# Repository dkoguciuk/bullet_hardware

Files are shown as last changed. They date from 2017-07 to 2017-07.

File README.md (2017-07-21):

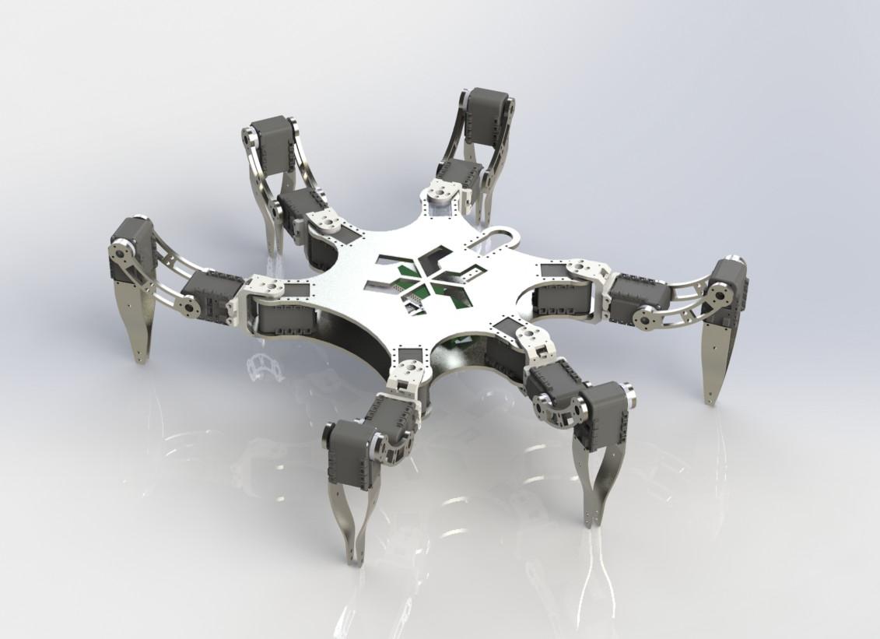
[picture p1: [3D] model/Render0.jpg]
asdasd


# Introduction

This is the project of a six-legged walking robot Bullet named after [bullet ant](http://en.wikipedia.org/wiki/Paraponera_clavata). The project consists of three repositories:
* [bullet_hardware](http://github.com/dkoguciuk/bullet_hardware) - containing 3D model of the robot done with SolidWorks and schematic and layout of PCB boards done with Eagle Software,
* [bullet_firmware](https://github.com/dkoguciuk/bullet_firmware) - containing a low-level program for STM microprocessor written for one of the PCB boards done with CooCox tool,
* [bullet_software](https://github.com/dkoguciuk/bullet_software) - containing a high-level software for onboard RaspberryPi board done with ROS Framework.

# MORE

More information on the [WIKI](http://github.com/dkoguciuk/bullet_software/wiki).

# License

"THE BEER-WARE LICENSE" (Revision 42):  
Above listed contributors are authors of the repositories. As long as you retain this notice you can do whatever you want with this stuff. If we meet some day, and you think this stuff is worth it, you can buy us a beer in return.

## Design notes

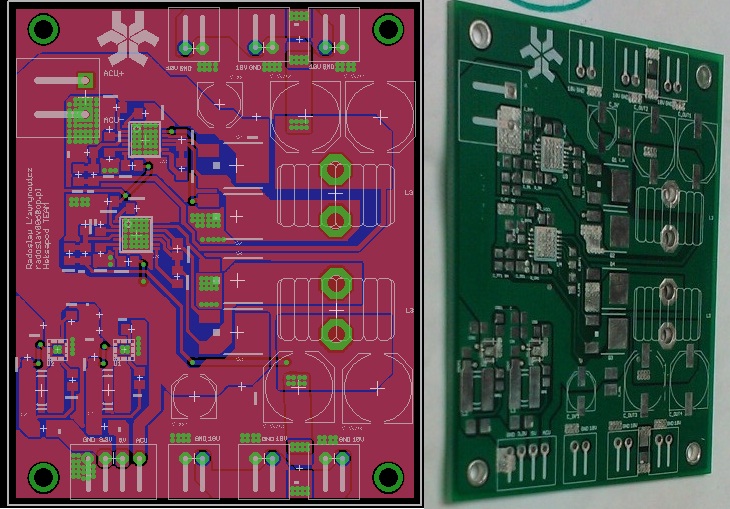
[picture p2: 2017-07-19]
[PCB] power_board/photos/img_fot.jpg

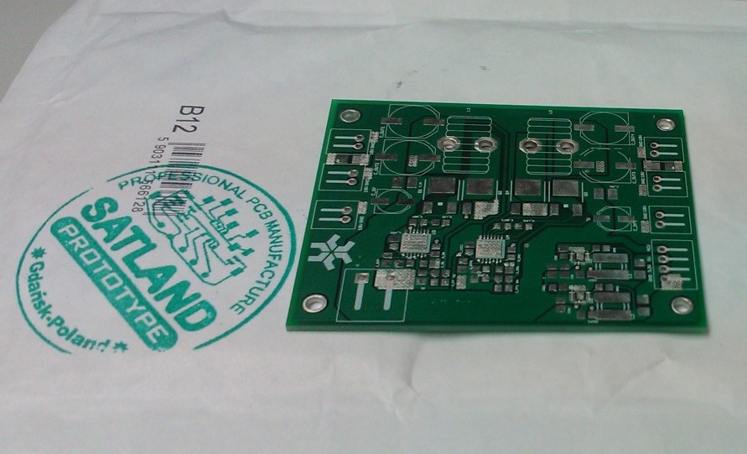
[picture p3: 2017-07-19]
[PCB] power_board/photos/PCB_foto1.jpg

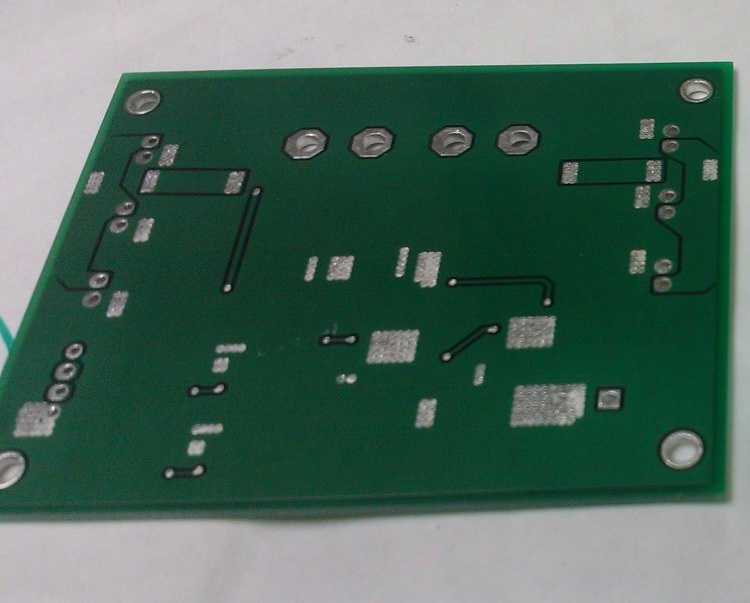
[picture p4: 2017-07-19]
[PCB] power_board/photos/PCB_foto2.jpg

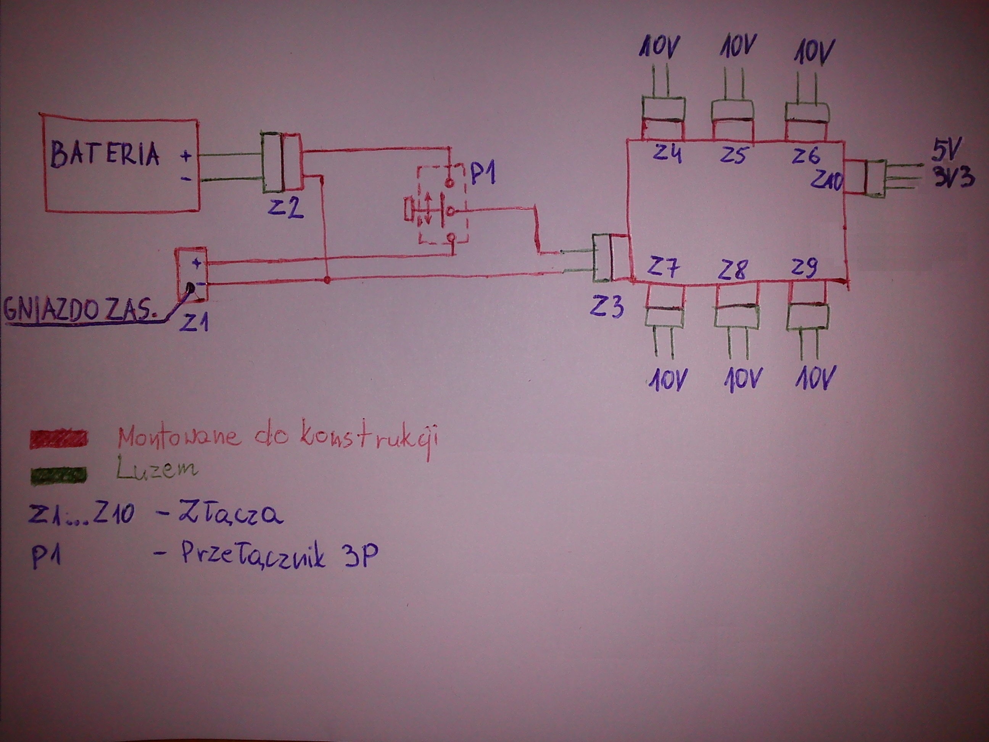
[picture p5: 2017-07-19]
[PCB] power_board/docs/power_sketch.jpg

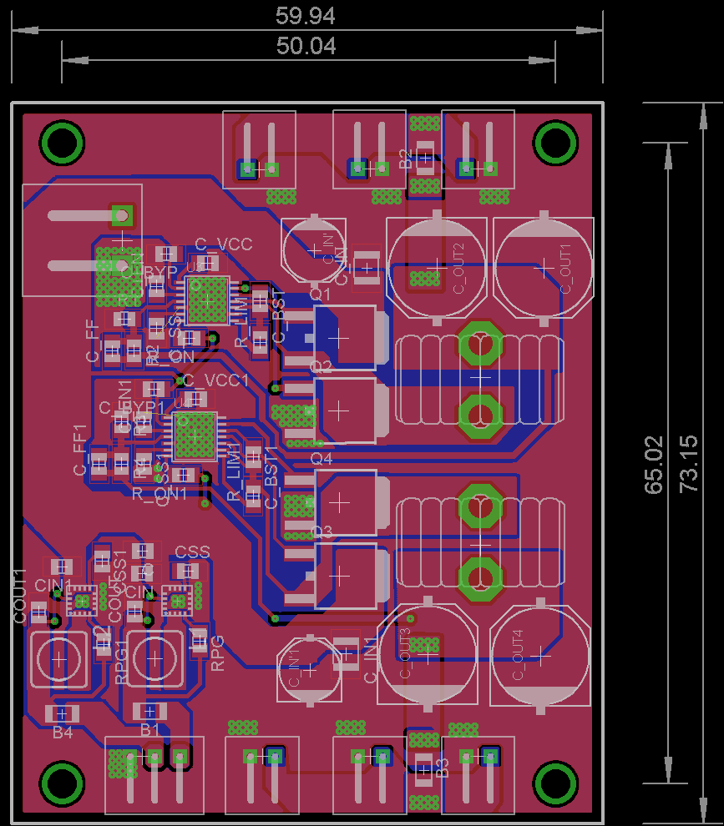
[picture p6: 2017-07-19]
[PCB] power_board/photos/img_płytka.png

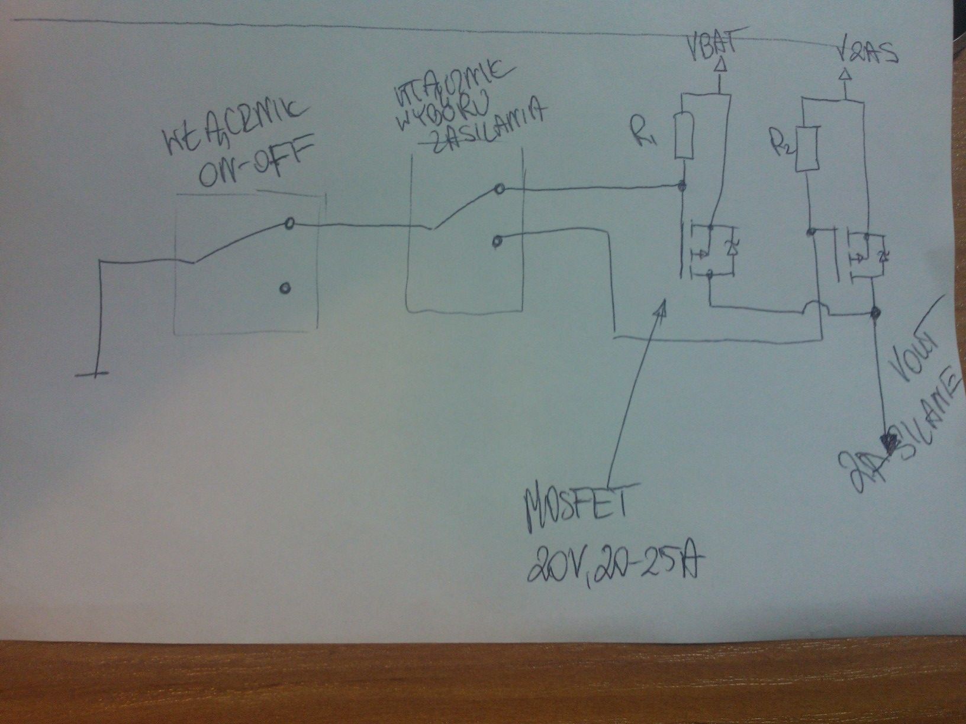
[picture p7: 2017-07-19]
[PCB] power_board/docs/switches_sketch.jpg

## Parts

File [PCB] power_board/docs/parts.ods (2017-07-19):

Nazwa | Element | Ilość | Link
Przełącznik ON-OFF-ON | P1 | 1 | http://www.tme.eu/pl/details/ae-c1720hoaaa/przelaczniki-dzwigniowe/arcolectric/c1720hobbi0ii/
Gniazdo zasilania 10V | Z4-Z9 | 6 | http://www.tme.eu/pl/details/mx-5268-02a/zlacza-spox/molex/0022057025-5268-02a/
Wtyk zasilania 10V | Z4-Z9 | 6 | http://www.tme.eu/pl/details/mx-5264-02/zlacza-spox/molex/0050375023-5264-02/#
Gniazdo zasilania 3.3V / 5V | Z10 | 1 | http://www.tme.eu/pl/details/mx-5268-03a/zlacza-spox/molex/0022057035-5268-03a/#
Wtyk zasilania 3.3V / 5V | Z10 | 1 | http://www.tme.eu/pl/details/mx-5264-03/zlacza-spox/molex/0050375033-5264-03/#
Styki wtyków 10V / 5V / 3.3V | Z4-Z10 | 15 | http://www.tme.eu/pl/details/mx-5263-pbtl/zlacza-spox/molex/0008701040-5263pbtl/#
Gniazdo zasilania wejściowe | Z3 | 1 | http://www.tme.eu/pl/details/2edgrc-5.0-02p14/listwy-zaciskowe-do-druku/degson-electronics/2edgrc-50-02p-14-00ah/
Wtyk zasilania wejściowego | Z3 | 1 | http://www.tme.eu/pl/details/2edgk5.00-02p14/listwy-zaciskowe-do-druku/degson-electronics/2edgk-500-02p-14/
Gniazdo + Wtyk zasilacza | Z1 | 1 | http://riku.pl/towar/p/id/1530/kontekst/4206/
Bezpiecznik 3.3V / 5V | B1 | 2 | http://www.tme.eu/pl/details/3413.0222.11/bezpieczniki-smd-1206-szybkie/schurter/#
Bezpiecznik 10V | B2,B3 | 2 | http://www.tme.eu/pl/details/3413.0328.11/bezpieczniki-smd-1206-zwloczne/schurter/#
 |  |  |  | ??

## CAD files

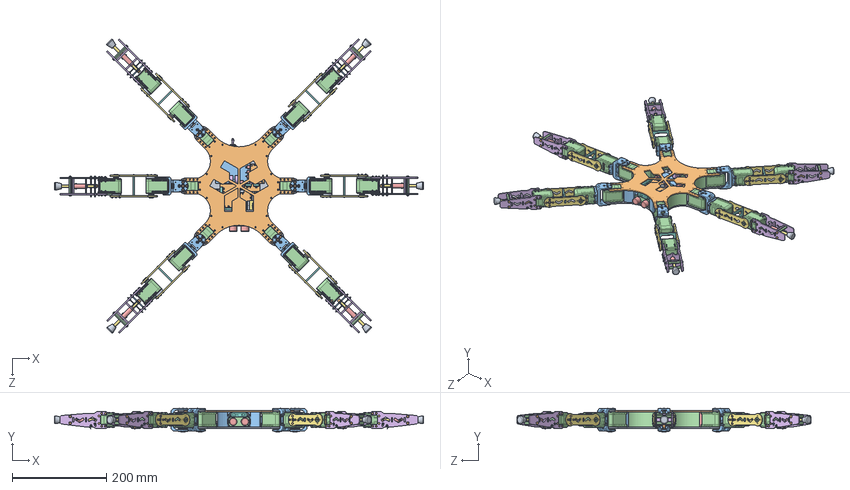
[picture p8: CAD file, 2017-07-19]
[3D] model/Bullet.SLDASM
784.4 x 50.1 x 625.7 mm
body_down
body_up
ax12_plastic_a x 6
ax12_body x 18
ax12_wheel x 18
ax12_cover x 72
ax12_connector x 36
ax12_insert x 18
ax12_horn x 18
ax12_screw x 18
ax12_plastic_b x 6
ax12_sleave x 18
ax12_ring x 18
forearm x 12
arm x 12
arm_strut x 6
omron_actuator x 6
omron_base x 6
rod_switch x 12
bushing x 12
sleeve_external x 6
forearm_strut x 12
sleeve_internal x 6
spring x 6
antislipper x 6
pan head cross recess screw_iso x 222
hex thin nut chamfered gradeab_iso x 72
sonar_pcb
sonar_transducer x 2
sonar_smt x 3
sonar_capacitor x 6
sharp_body
sharp_board
sharp_connector
plug_front
plug_side x 4
plug_rear
switch
switch_nut
imu_goldpin
imu_connector
imu_board
power_pcb
power_connector
power_molex_2 x 6
power_coil x 2
rpi_pcb
rpi_usb_5v
rpi_sd
rpi_gpio
rpi_usb_2x
rpi_lan
rpi_rca
rpi_jack
rpi_hdmi
stm_molex_4 x 9
stm_molex_3 x 5
stm_brd

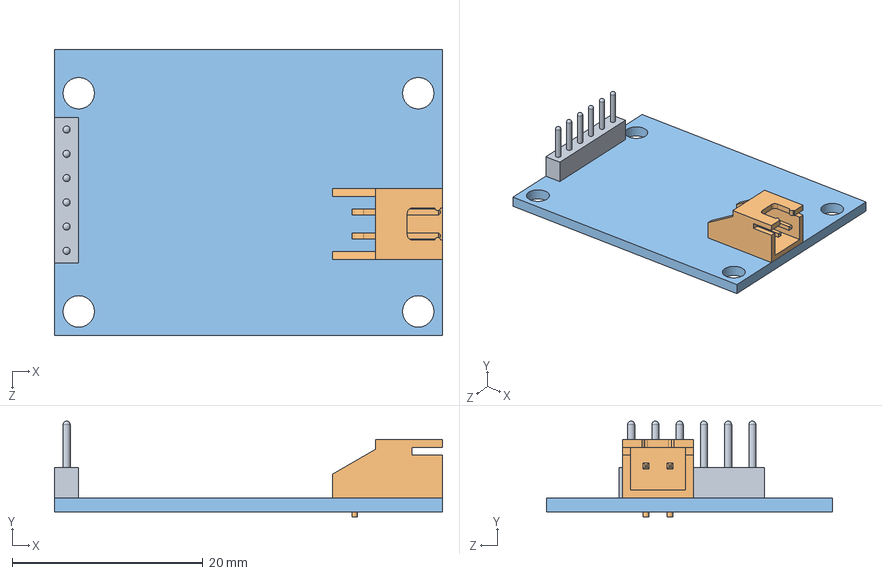
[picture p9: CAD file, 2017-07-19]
[3D] model/Electronics/IMU/imu.SLDASM
40.6 x 10.1 x 30.0 mm
imu_goldpin
imu_connector
imu_board

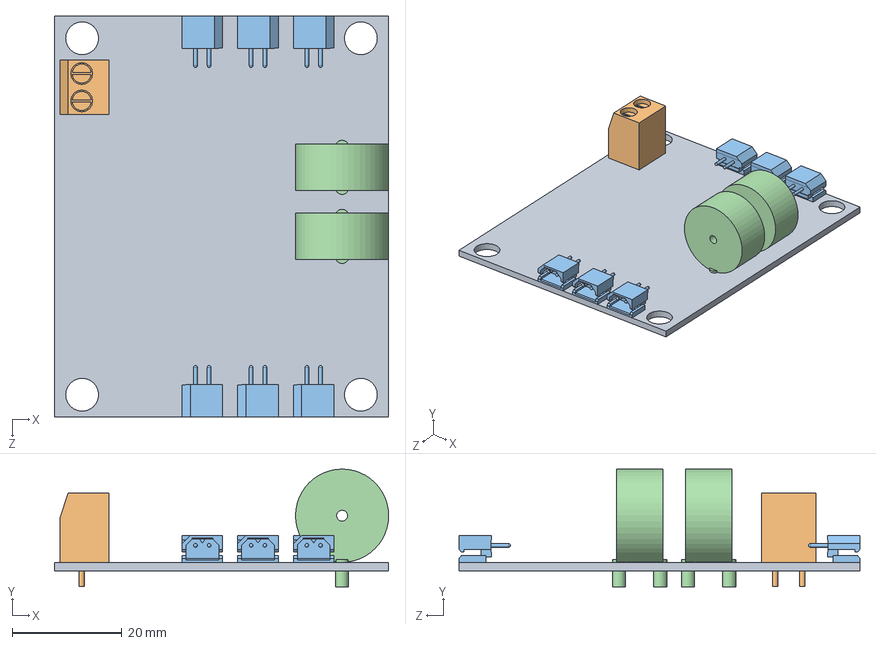
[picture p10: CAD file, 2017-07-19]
[3D] model/Electronics/PowerSupply/power_supply.SLDASM
61.0 x 21.5 x 73.2 mm
power_pcb
power_connector
power_molex_2 x 6
power_coil x 2

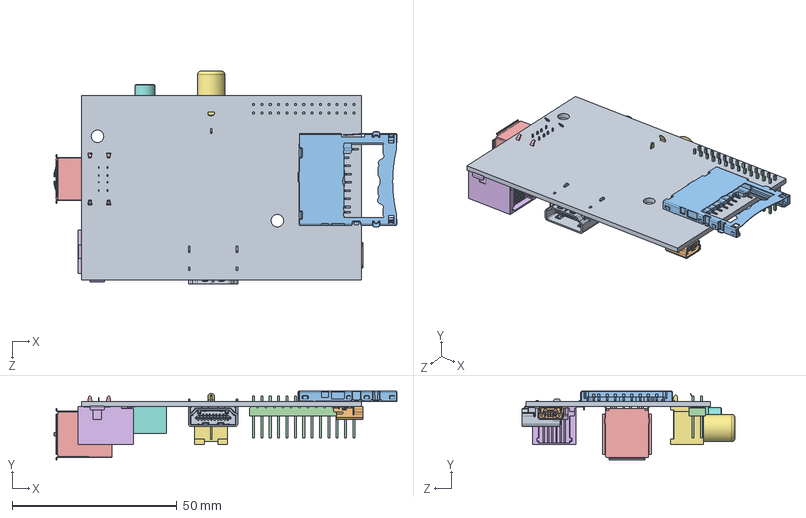
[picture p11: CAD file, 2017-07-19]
[3D] model/Electronics/RPI/rpi.SLDASM
104.1 x 20.9 x 64.6 mm
rpi_pcb
rpi_usb_5v
rpi_sd
rpi_gpio
rpi_usb_2x
rpi_lan
rpi_rca
rpi_jack
rpi_hdmi

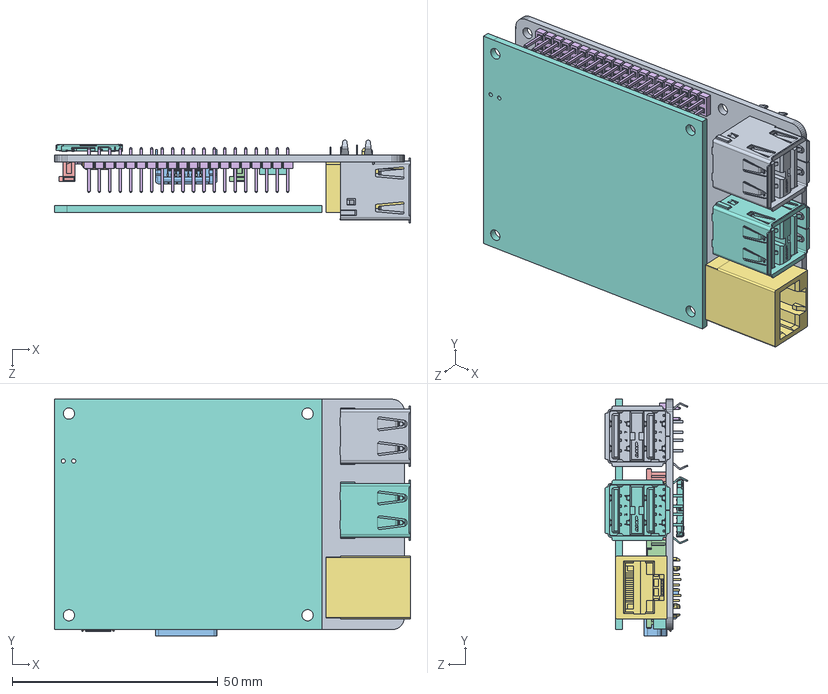
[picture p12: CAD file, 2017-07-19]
[3D] model/Electronics/RPI2/RPIBPlus.SLDASM
86.5 x 57.5 x 20.1 mm
Board
User_Library-0805_SMD_Resistor x 3
RES0402 x 53
CAPC1005X55N_EIA_0402 x 22
CAPC2012X90N_EIA_0805 x 12
CAPC3216X140N_EIA_1206
CAPC1608X55N_EIA_0603 x 4
c-2201778-1-a-3d
SMSCLAN9514
micro_usb
CSI
DSI
Samtec-TSW-120-07-F-D
USB
USB2
Extruded x 4
Extruded_2
Extruded_3 x 2
Extruded_4 x 2
Extruded_5
Extruded_6 x 2
Extruded_7
Extruded_8
Extruded_9 x 2
Extruded_10
Extruded_11
Extruded_12
Extruded_13 x 2
Extruded_14
BoardHelp

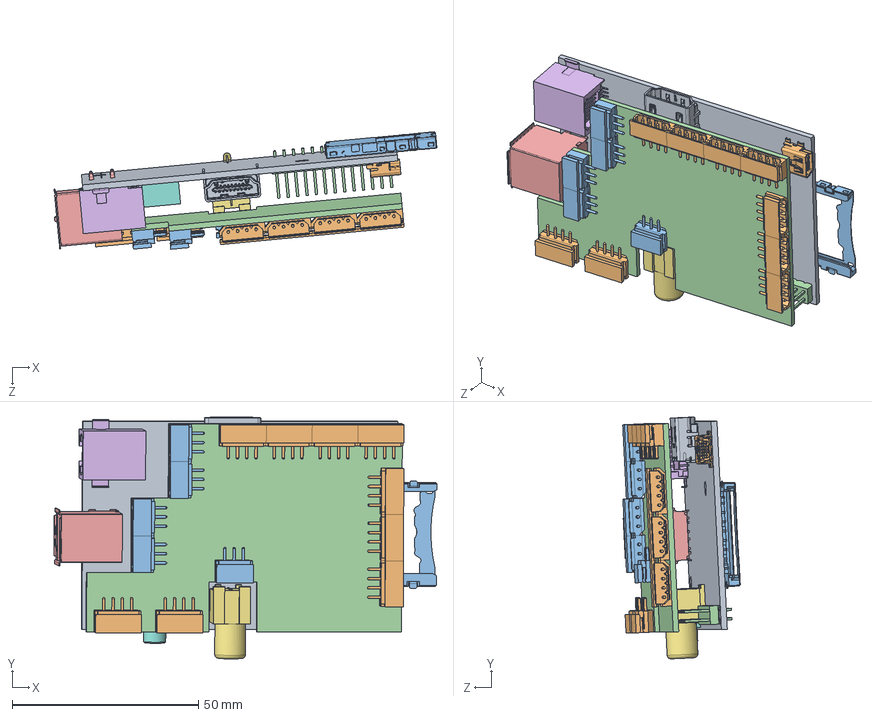
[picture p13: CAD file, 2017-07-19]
[3D] model/Electronics/STM/stm.SLDASM
102.9 x 65.0 x 31.6 mm
rpi_pcb
rpi_usb_5v
rpi_sd
rpi_gpio
rpi_usb_2x
rpi_lan
rpi_rca
rpi_jack
rpi_hdmi
stm_molex_4 x 9
stm_molex_3 x 5
stm_brd

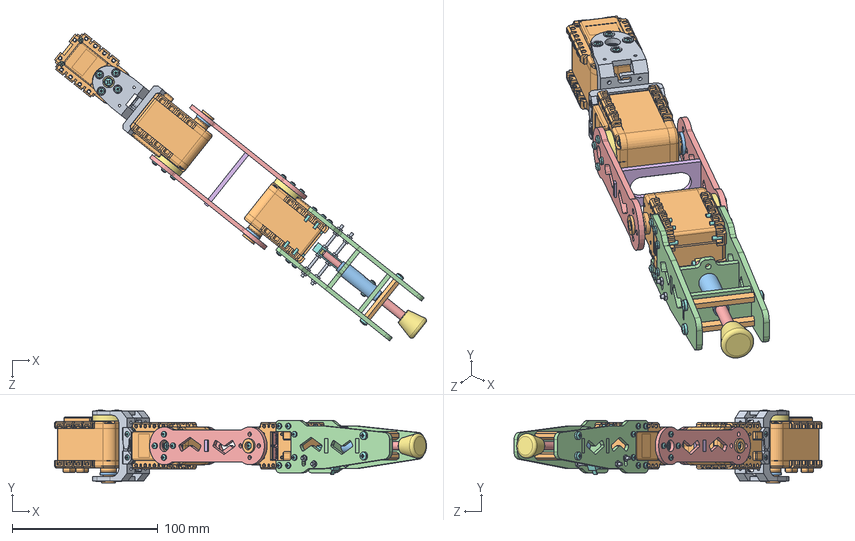
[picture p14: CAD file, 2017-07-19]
[3D] model/Leg/leg.SLDASM
255.4 x 50.1 x 211.4 mm
ax12_plastic_a
ax12_body x 3
ax12_wheel x 3
ax12_cover x 12
ax12_connector x 6
ax12_insert x 3
ax12_horn x 3
ax12_screw x 3
ax12_plastic_b
ax12_sleave x 3
ax12_ring x 3
forearm x 2
arm x 2
arm_strut
omron_actuator
omron_base
rod_switch x 2
bushing x 2
sleeve_external
forearm_strut x 2
sleeve_internal
spring
antislipper
pan head cross recess screw_iso x 37
hex thin nut chamfered gradeab_iso x 12

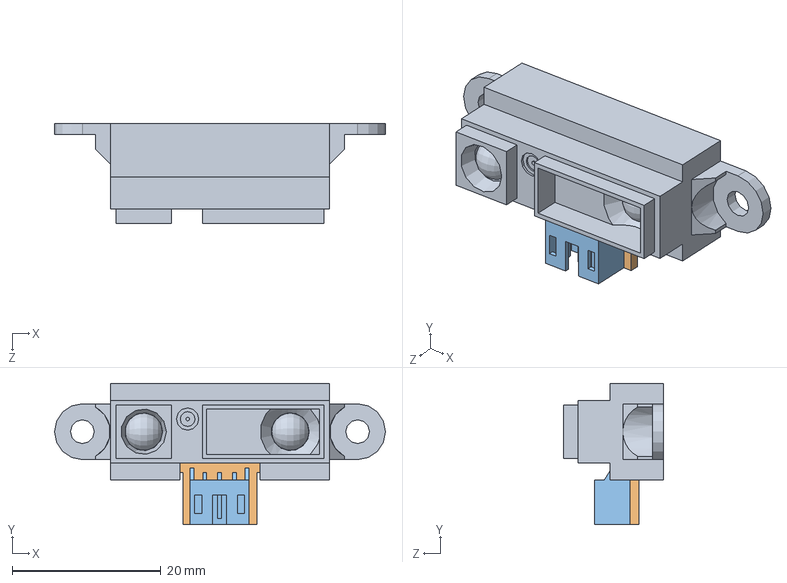
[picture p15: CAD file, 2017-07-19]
[3D] model/Electronics/Sharp/sharp.sldasm
44.5 x 19.0 x 13.5 mm
sharp_body
sharp_board
sharp_connector

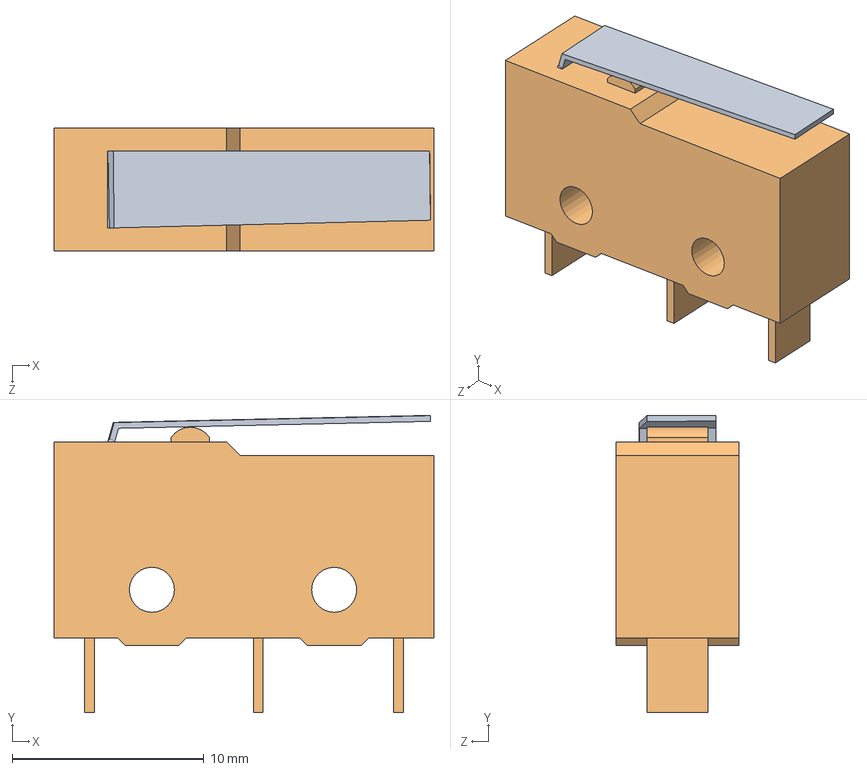
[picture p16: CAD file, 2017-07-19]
[3D] model/Leg/Omron/omron.SLDASM
19.8 x 15.5 x 6.40 mm
omron_actuator
omron_base

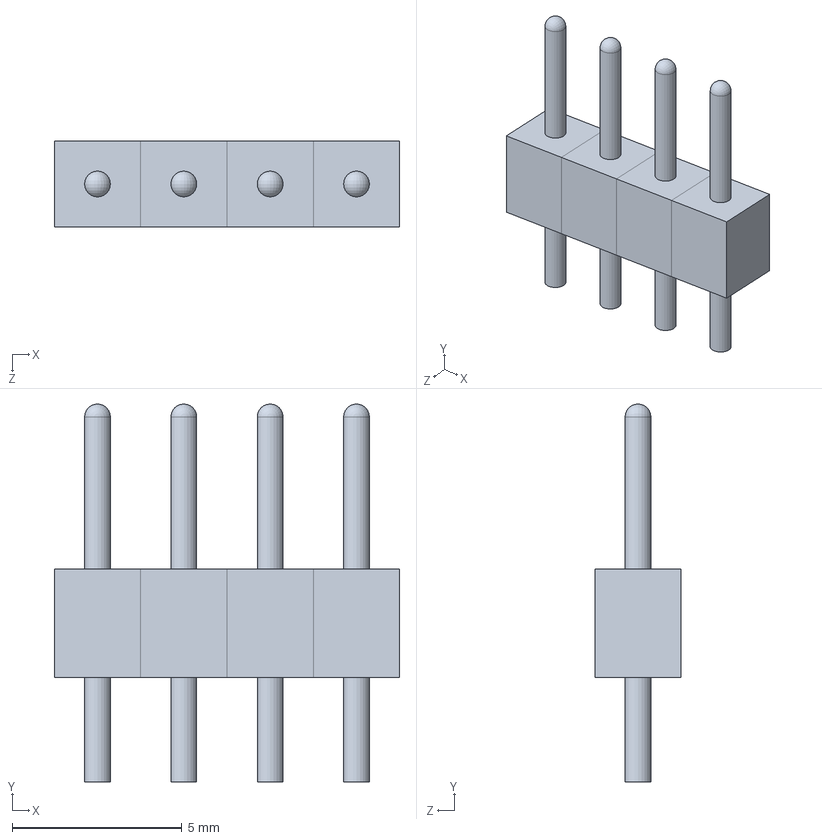
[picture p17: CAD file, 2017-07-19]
[3D] model/Electronics/STM/Parts/stm_goldpin_4.SLDASM
10.2 x 11.1 x 2.54 mm
GoldPin1x x 4

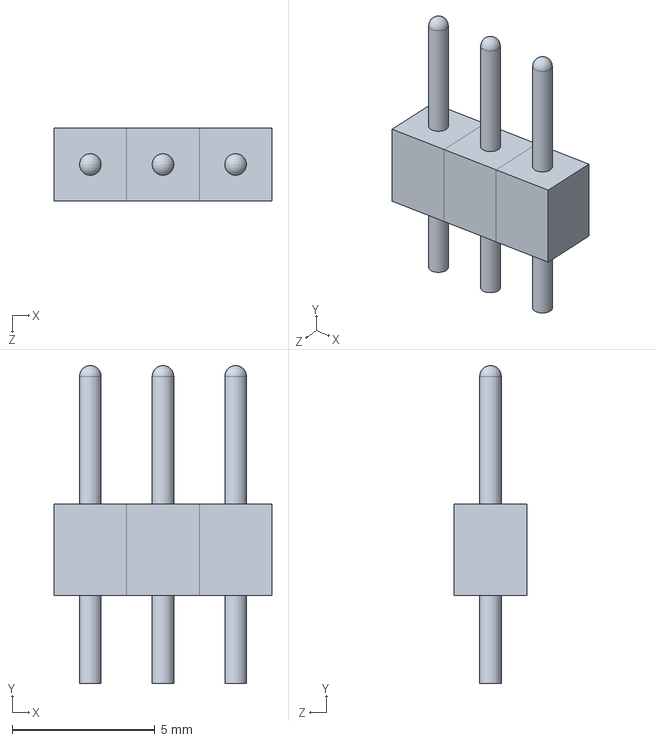
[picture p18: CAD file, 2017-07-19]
[3D] model/Electronics/STM/Parts/stm_goldpin_3.SLDASM
7.62 x 11.1 x 2.54 mm
GoldPin1x x 3

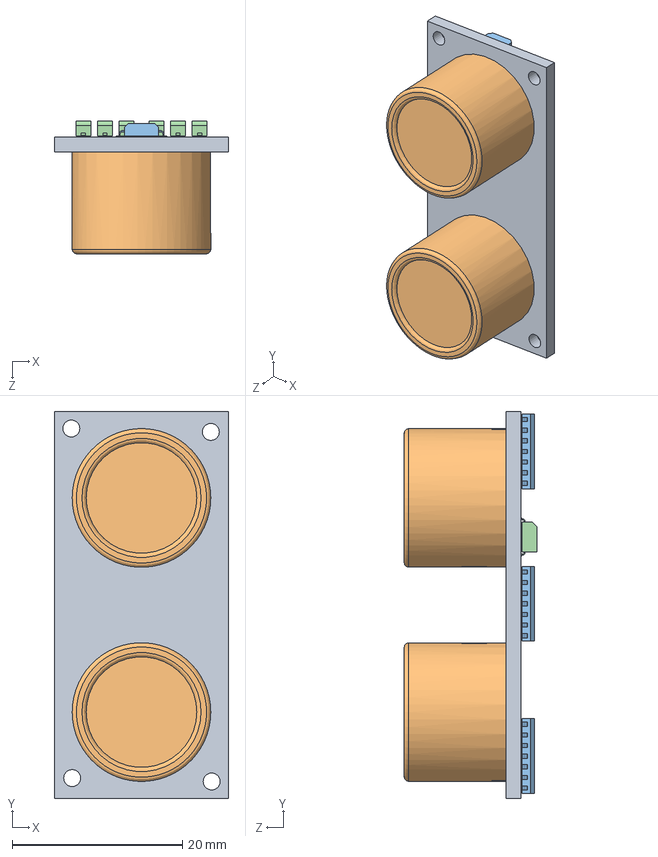
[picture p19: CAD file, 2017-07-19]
[3D] model/Electronics/Sonar/sonar.SLDASM
20.5 x 45.5 x 15.6 mm
sonar_pcb
sonar_transducer x 2
sonar_smt x 3
sonar_capacitor x 6

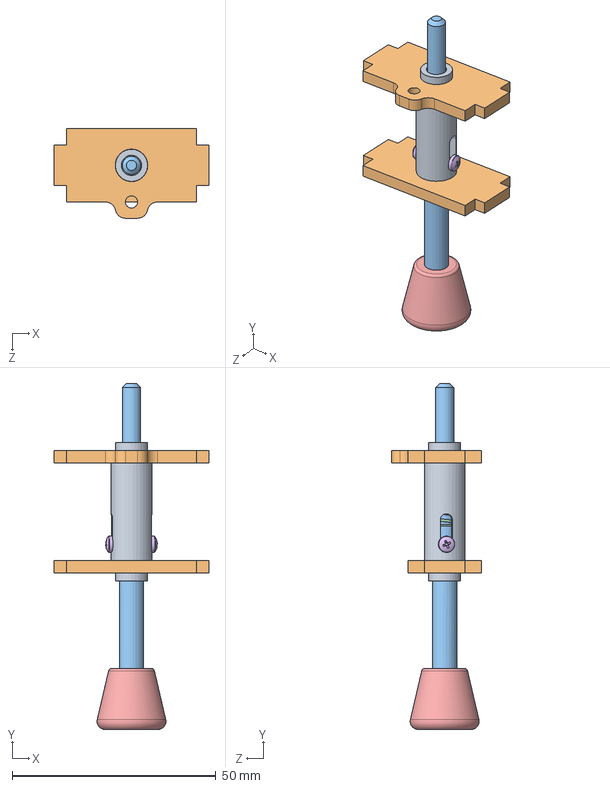
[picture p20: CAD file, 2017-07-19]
[3D] model/Leg/Absorber/absorber.SLDASM
38.0 x 85.0 x 22.0 mm
sleeve_external
forearm_strut x 2
sleeve_internal
spring
antislipper
pan head cross recess screw_iso x 2

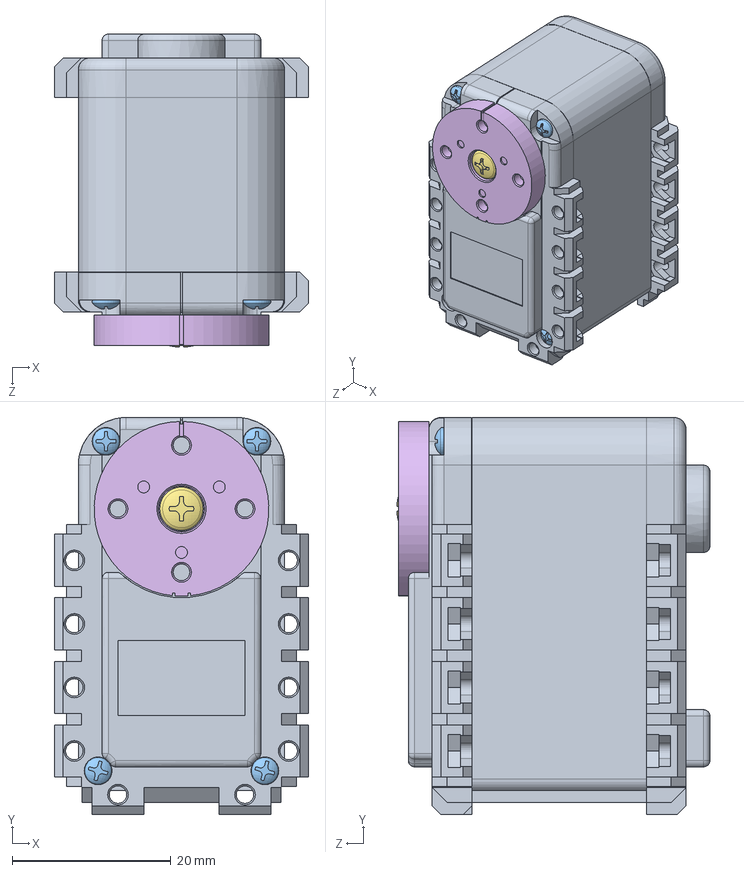
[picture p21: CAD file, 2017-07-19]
[3D] model/Leg/AX-12A/ax12.SLDASM
32.0 x 50.0 x 39.4 mm
ax12_body
ax12_wheel
ax12_cover x 4
ax12_connector x 2
ax12_insert
ax12_horn
ax12_screw

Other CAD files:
[3D] model/Electronics/RPI2/Parts/HDMI.sldasm
[3D] model/Electronics/RPI2/Parts/Ethernet.sldasm
[3D] model/Electronics/RPI2/Parts/Free-Models.sldasm
[3D] model/CAM/arm_strut_final_3.dxf
[3D] model/Body/body_down.SLDPRT
[3D] model/Body/body_up.SLDPRT
[3D] model/Body/plug_front.sldprt
[3D] model/Body/plug_rear.sldprt
[3D] model/Body/plug_side.sldprt
[3D] model/Body/switch.SLDPRT
[3D] model/Body/switch_nut.SLDPRT
[3D] model/CAM/arm_final_3.dxf
[3D] model/CAM/body_bottom_final_3.dxf
[3D] model/CAM/body_top_final_3.dxf
[3D] model/CAM/forearm_final_3.dxf
[3D] model/CAM/forearm_strut_A_final_3.dxf
[3D] model/CAM/forearm_strut_B_final_3.dxf
[3D] model/CAM/sleeve_external_final_3.dxf
[3D] model/CAM/sleeve_internal_final_3.dxf
[3D] model/Electronics/Battery/battery.SLDPRT
[3D] model/Electronics/IMU/Parts/imu_board.SLDPRT
[3D] model/Electronics/IMU/Parts/imu_connector.SLDPRT
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

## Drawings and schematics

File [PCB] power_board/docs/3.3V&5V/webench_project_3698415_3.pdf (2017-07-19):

# WEBENCH® Power Architect

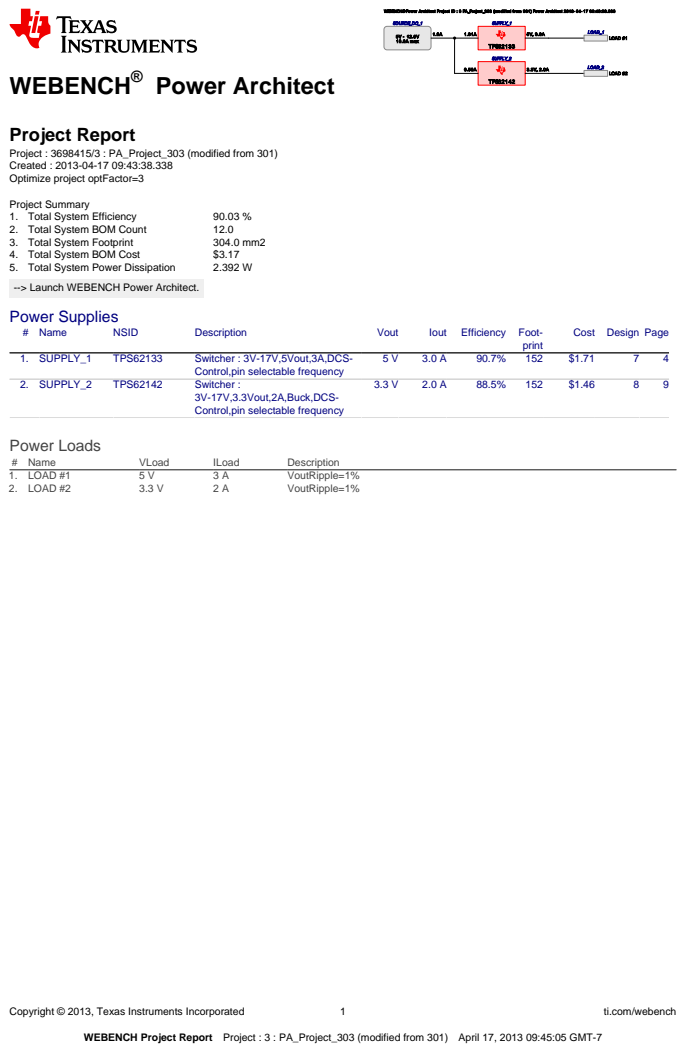
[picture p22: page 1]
Copyright © 2013, Texas Instruments Incorporated; ti.com/webench; 1. Total System Efficiency; 2. Total System BOM Count; 3. Total System Footprint; 4. Total System BOM Cost; 5. Total System Power Dissipation; LOAD_1; LOAD #1; TPS62133; SUPPLY_1; LOAD_2; LOAD #2; TPS62142; SUPPLY_2; 9V - 12.6V 10.0A max; SOURCE_DC_1; # Name; NSID; Description; Vout; Iout Efficiency Foot-; print; 1. SUPPLY_1; Switcher : 3V-17V,5Vout,3A,DCS-; 2. SUPPLY_2; Switcher :; Power Loads; VLoad; ILoad; 1. LOAD #1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

WEBENCH® Power Architect Project ID : 3 PA_Project_303 (modified from 301) Power Architect 2013- 04- 17 09:43:38.338

Project Report
Project : 3698415/3 : PA_Project_303 (modified from 301)
Created : 2013-04-17 09:43:38.338
Optimize project optFactor=3

Project Summary
--> Launch WEBENCH Power Architect. (http://webench.ti.com/webench5/power/webench5.cgi?app=powerarchitect&project_id=3)
Power Supplies

Cost Design Page

Control,pin selectable frequency

3V-17V,3.3Vout,2A,Buck,DCS-

WEBENCH Project Report Project : 3 : PA_Project_303 (modified from 301) April 17, 2013 09:45:05 GMT-7

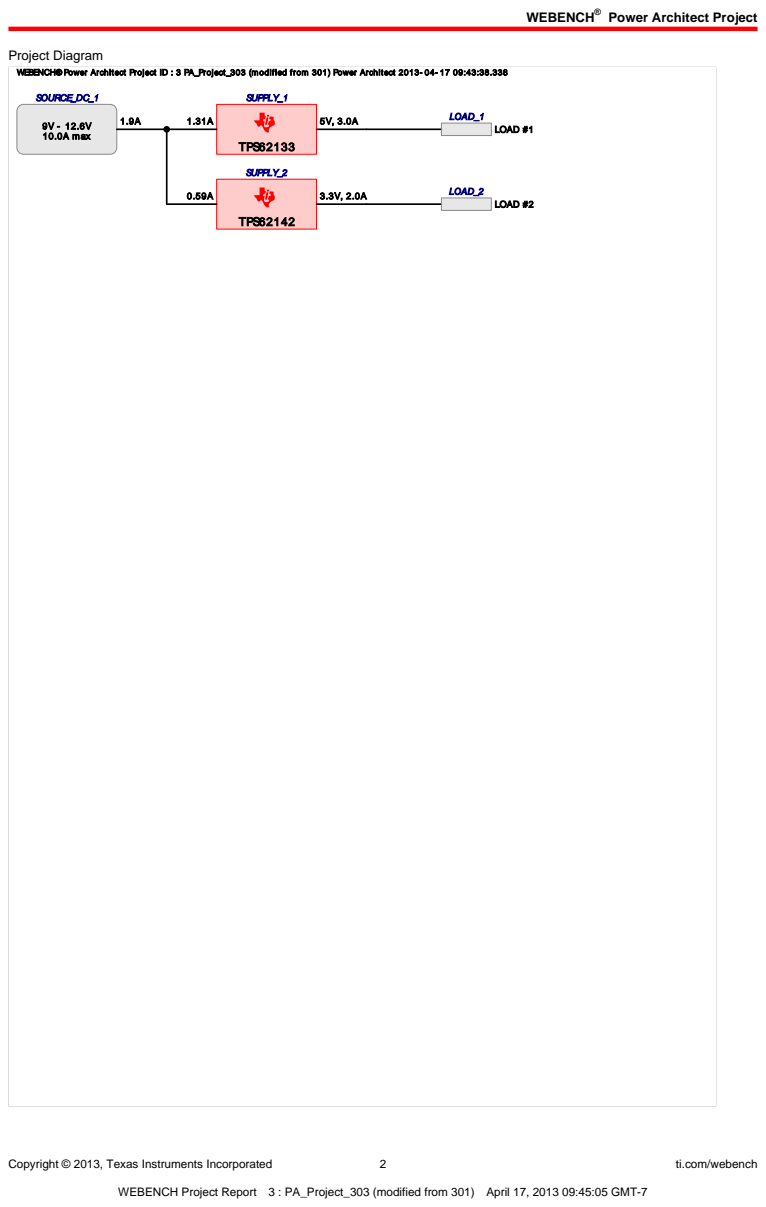
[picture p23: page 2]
WEBENCH®; Copyright © 2013, Texas Instruments Incorporated; ti.com/webench; Project Diagram; LOAD_1; LOAD #1; TPS62133; SUPPLY_1; LOAD_2; LOAD #2; TPS62142; SUPPLY_2; 9V - 12.6V 10.0A max; SOURCE_DC_1

Power Architect Project

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

WEBENCH Project Report 3 : PA_Project_303 (modified from 301) April 17, 2013 09:45:05 GMT-7

Copyright © 2013, Texas Instruments Incorporated | 3 | ti.com/webench

### Electrical Procurement BOM

Manufacturer | Part Number | Description | Quantity Budgetary Price | Footprint
(mm²
)
Kemet | C0805C332K5RACTU | 0805 | 2 | $0.01 | 26
TDK | C2012X5R0J226M | 0805 | 1 | $0.06 | 13
Vishay-Dale | CRCW0402100KFKED | 0402 | 2 | $0.01 | 15
MuRata | GRM31CR61E106KA12L | 1206 | 2 | $0.07 | 37
Taiyo Yuden | LMK212BJ226MG-T | 0805 | 1 | $0.12 | 13
Bourns | SRN6045-2R2Y | SRN6045 | 1 | $0.16 | 64
Texas Instruments | TPS62133RGTR | S-PVQFN-N16 | 1 | $1.30 | 36
Texas Instruments | TPS62142RGTR | S-PVQFN-N16 | 1 | $1.15 | 36
TDK | VLC6045T-2R2N | VLC6045 | 1 | $0.20 | 64
Total | | | 12 | $3.17 | 304

## WEBENCH ® Design Report

## TPS62133

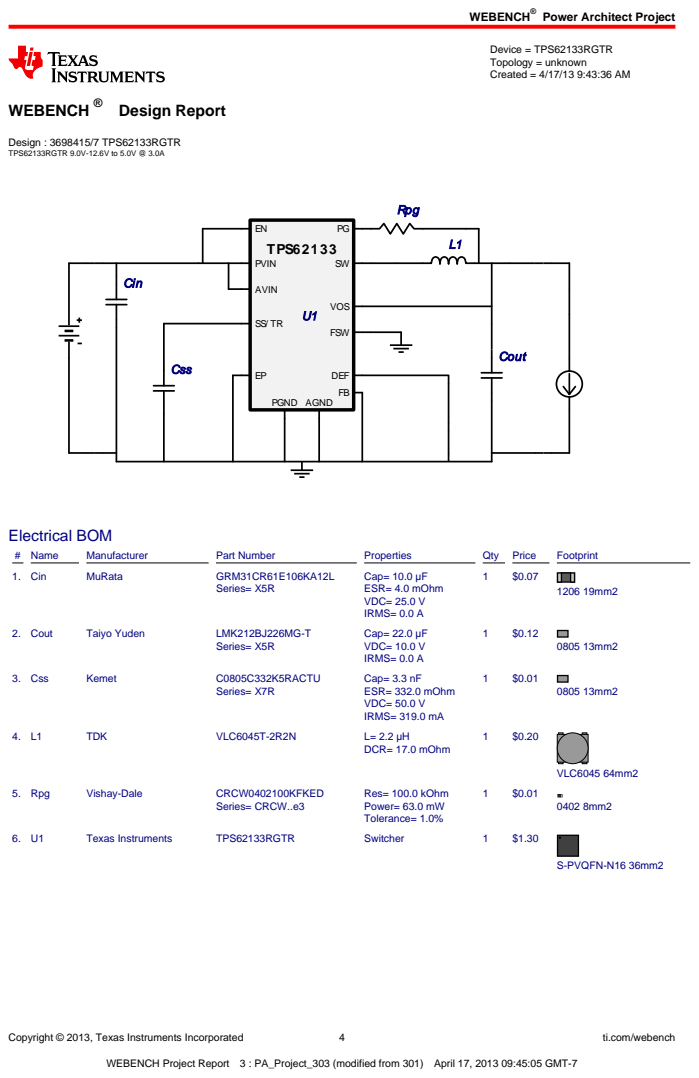
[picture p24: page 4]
Copyright © 2013, Texas Instruments Incorporated; ti.com/webench; Design : 3698415/7 TPS62133RGTR TPS62133RGTR 9.0V-12.6V to 5.0V @ 3.0A; Device = TPS62133RGTR Topology = unknown Created = 4/17/13 9:43:36 AM; Cin; Cout; Css; Rpg; AGND; FSW; DEF; AVIN; PVIN; VOS; PGND; Electrical BOM; # Name; Manufacturer; Part Number; Properties; Qty Price; Footprint; 1. Cin; MuRata; GRM31CR61E106KA12L; Series= X5R; Cap= 10.0 µF ESR= 4.0 mOhm VDC= 25.0 V IRMS= 0.0 A; 2. Cout; Taiyo Yuden; LMK212BJ226MG-T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

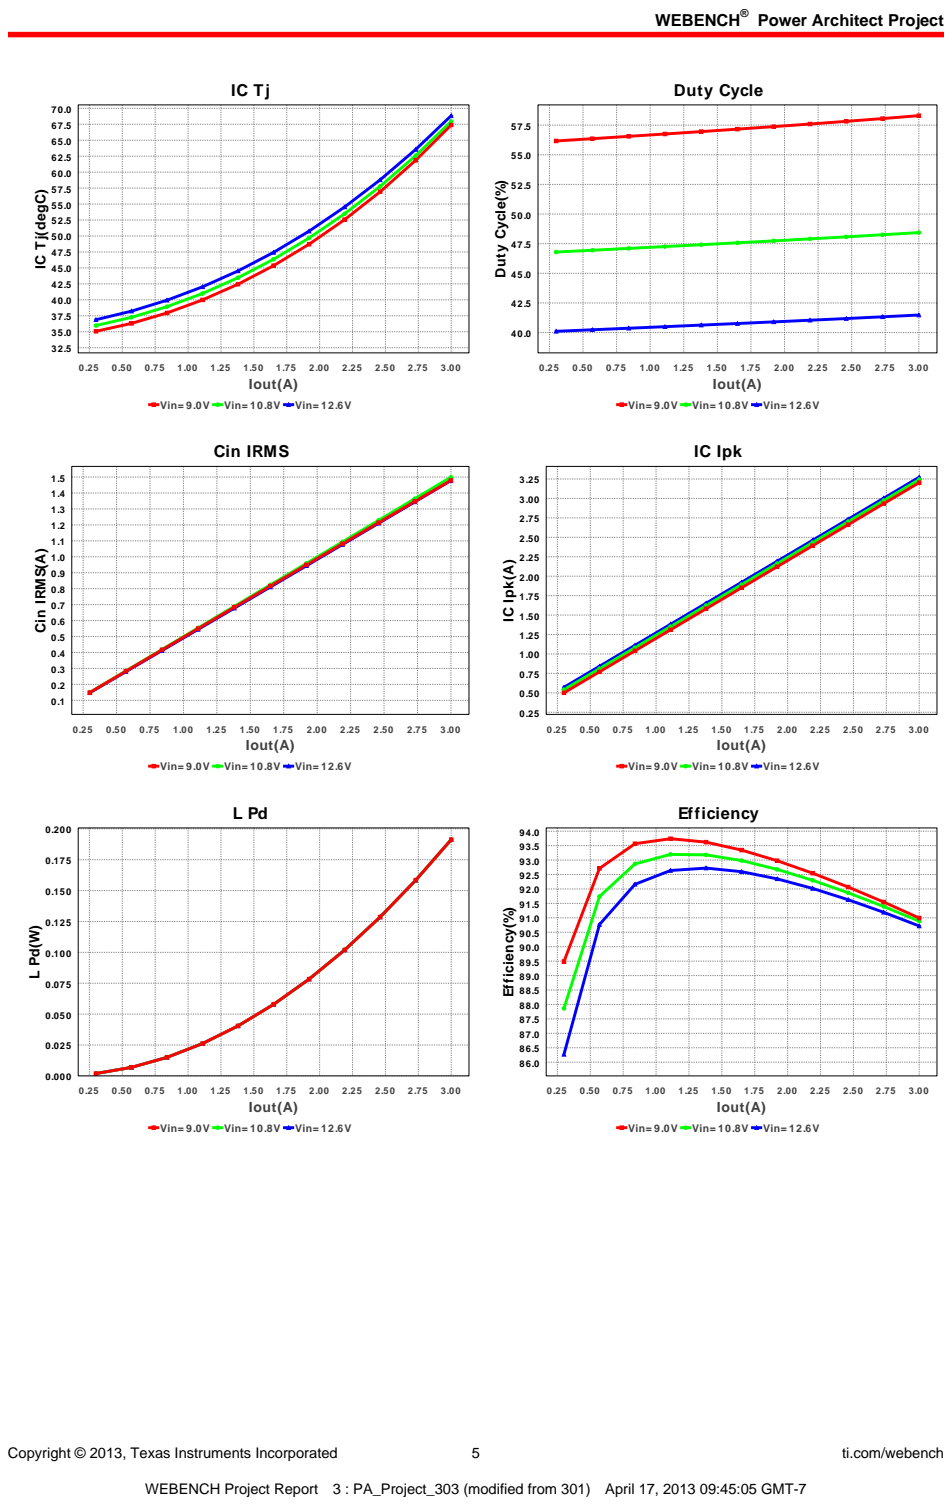
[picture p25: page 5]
Copyright © 2013, Texas Instruments Incorporated; ti.com/webench; 0.25 0.50 0.75 1.00 1.25 1.50 1.75 2.00 2.25 2.50 2.75 3.00 Iout(A); Duty Cycle; Iout(A); Duty Cycle(%); Cin IRMS; Cin IRMS(A); IC Ipk; IC Ipk(A); Efficiency; Efficiency(%)

IC Tj(degC)

Vin= 9.0V Vin= 10.8V Vin= 12.6V

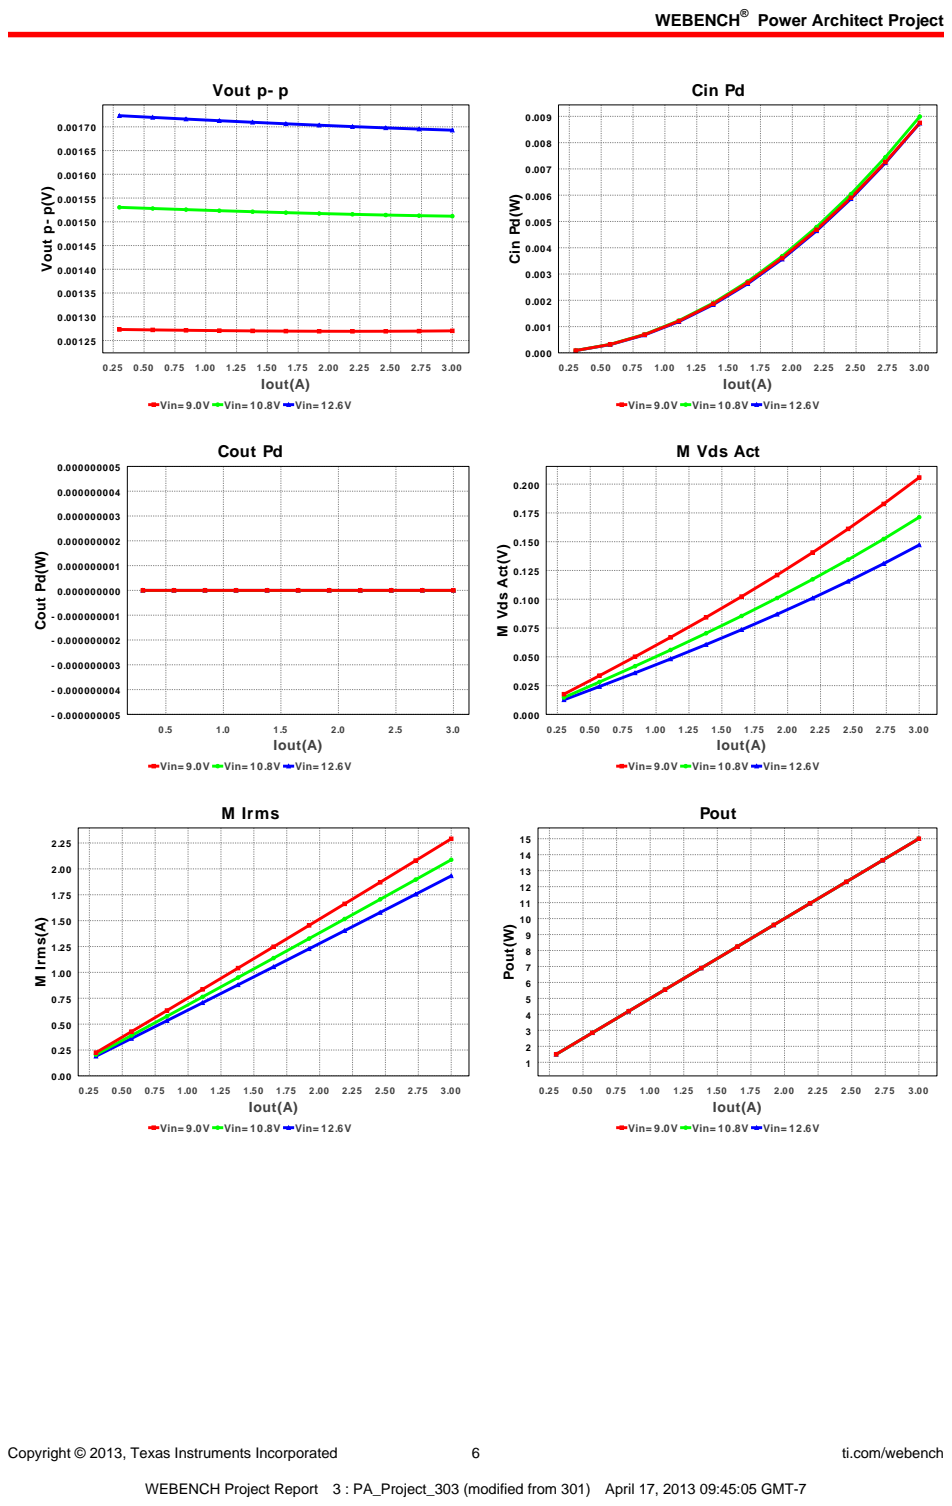
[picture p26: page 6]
Copyright © 2013, Texas Instruments Incorporated; ti.com/webench; Vout p- p; 0.25 0.50 0.75 1.00 1.25 1.50 1.75 2.00 2.25 2.50 2.75 3.00 Iout(A); Vout p- p(V); Cin Pd; Cin Pd(W); Cout Pd; Iout(A); Cout Pd(W); M Vds Act; M Vds Act(V); M Irms; M Irms(A); Pout; Pout(W)

Vin= 9.0V Vin= 10.8V Vin= 12.6V

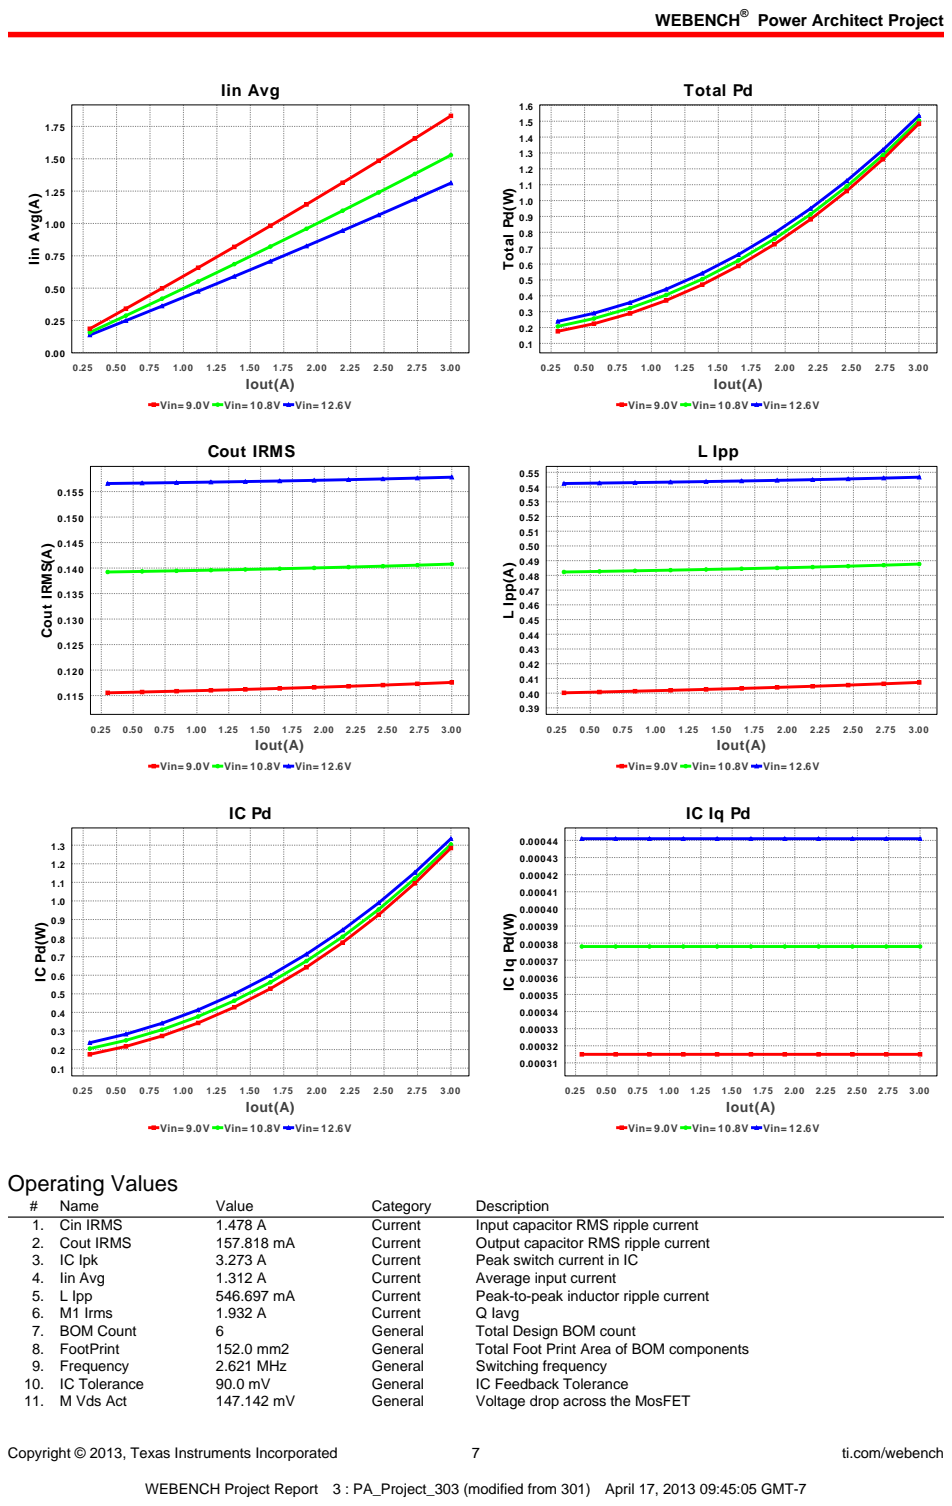
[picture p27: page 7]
Copyright © 2013, Texas Instruments Incorporated; ti.com/webench; Iin Avg; Iout(A); Iin Avg(A); Total Pd; Total Pd(W); Cout IRMS; 0.25 0.50 0.75 1.00 1.25 1.50 1.75 2.00 2.25 2.50 2.75 3.00 Iout(A); Cout IRMS(A); L Ipp; L Ipp(A); Operating Values; Name; Value; Category; Description; 1. Cin IRMS; Current; Input capacitor RMS ripple current; 2. Cout IRMS; Output capacitor RMS ripple current; 3. IC Ipk; Peak switch current in IC; 4. Iin Avg; Average input current; 5. L Ipp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

Vin= 9.0V Vin= 10.8V Vin= 12.6V

Copyright © 2013, Texas Instruments Incorporated | 8 | ti.com/webench
# | Name | Value | Category | Description

12. Mode | CCM | General | Conduction Mode
13. Pout | 15.0 W | General | Total output power
14. Total BOM | $1.71 | General | Total BOM Cost
15. Vout OP | 5.0 V | Op_Point | Operational Output Voltage
16. Duty Cycle | 41.481 % | Op_point | Duty cycle
17. Efficiency | 90.717 % | Op_point | Steady state efficiency
18. IC Tj | 68.846 degC | Op_point | IC junction temperature
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

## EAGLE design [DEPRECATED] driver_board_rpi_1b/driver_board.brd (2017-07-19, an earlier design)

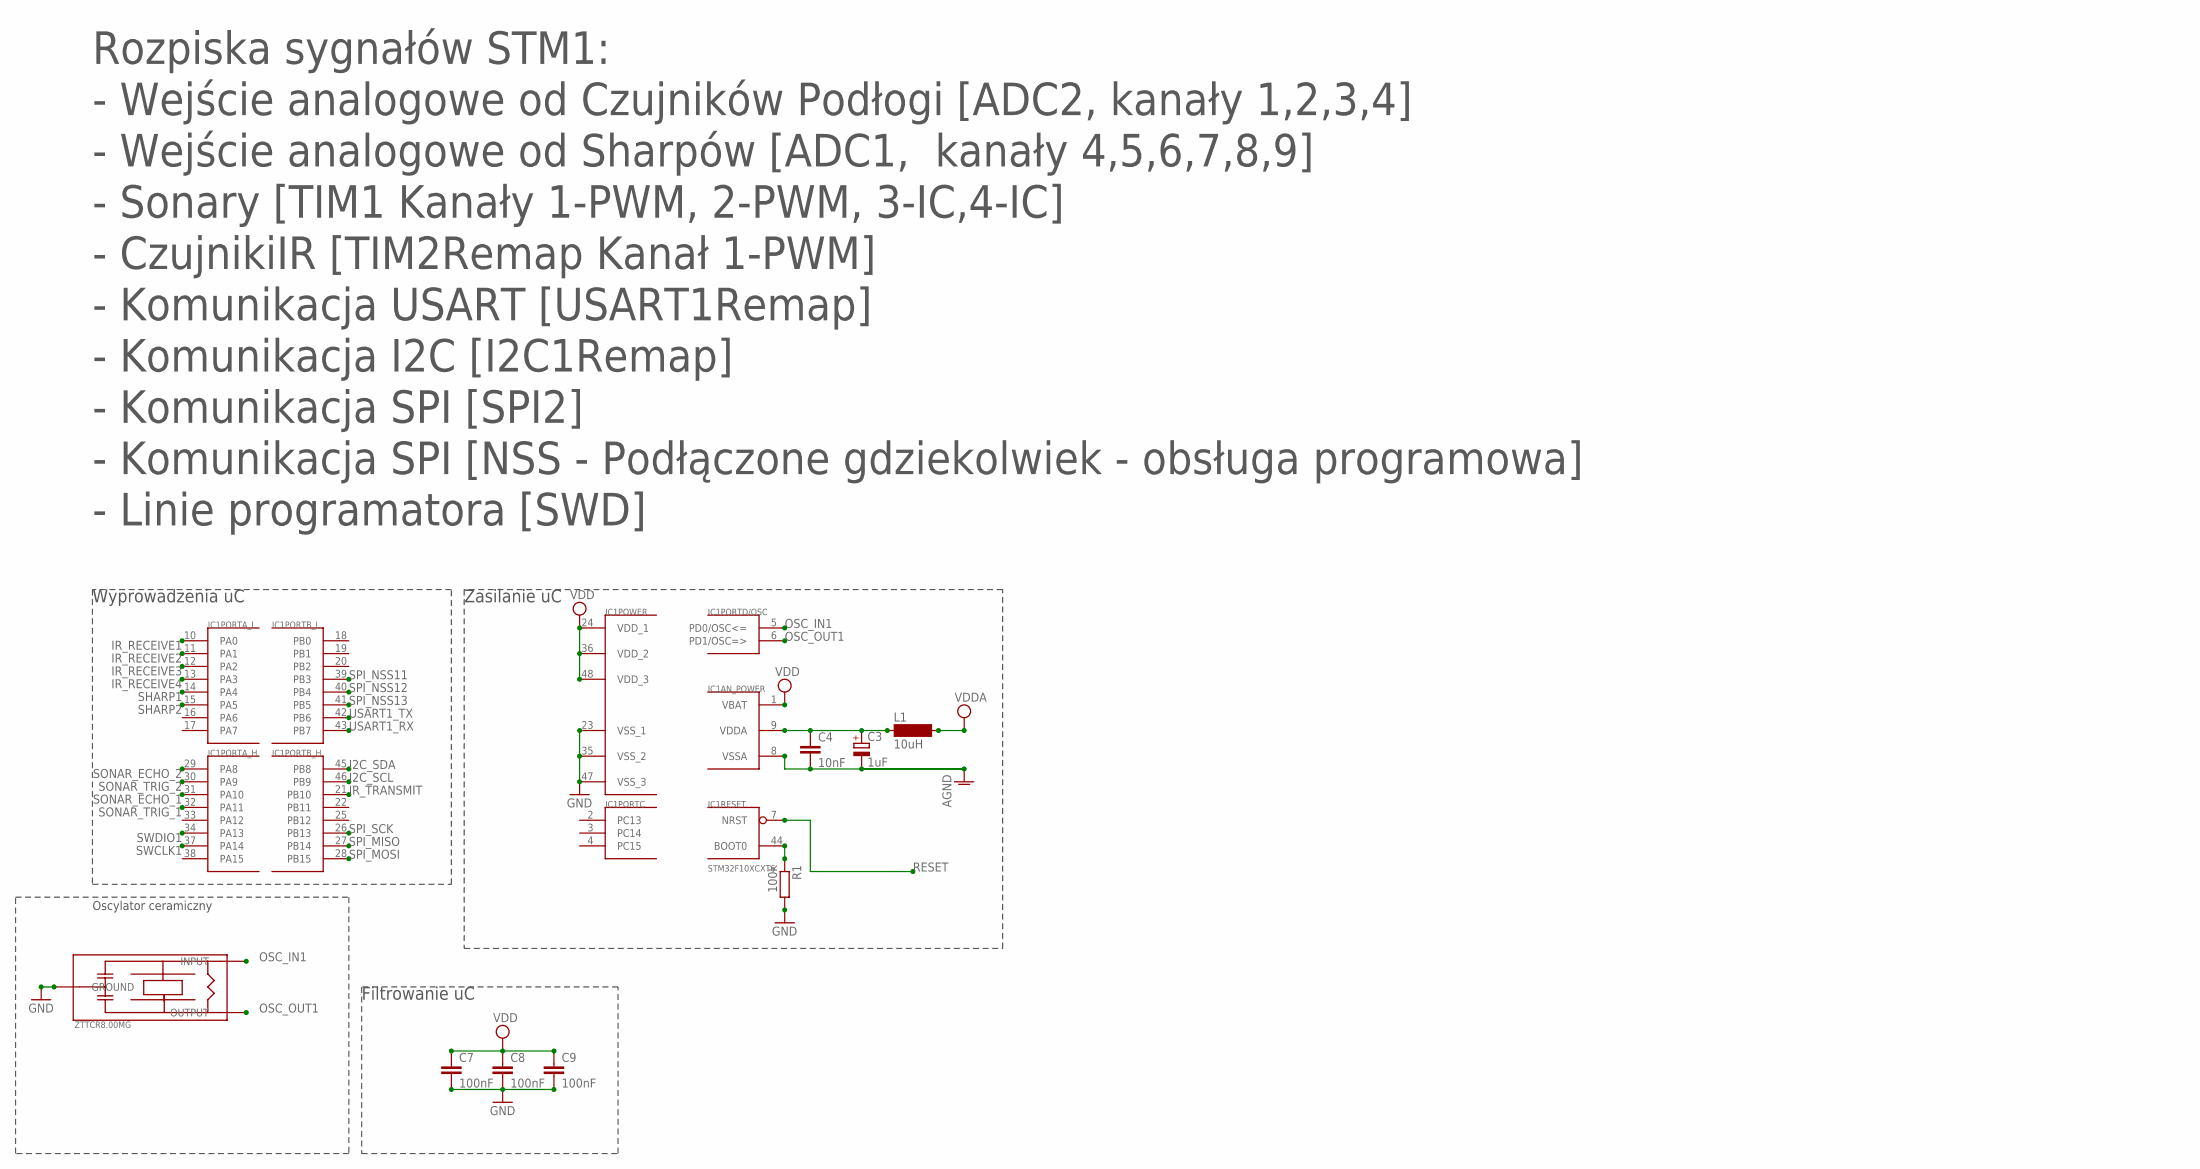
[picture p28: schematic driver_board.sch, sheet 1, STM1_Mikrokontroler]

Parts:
C3: 1uF; SMC_A
C4: 10nF; C0805
C7, C8, C9: 100nF; C0805
IC1: STM32F10XCXT6; TQFP48
L1: 10uH; SM-1206
R1: 100k; R0805
U$7: ZTTCR8.00MG

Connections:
AGND: C3.-, C4.2, IC1.8 (VSSA); also elsewhere on the board
GND: C7.2, C8.2, C9.2, IC1.23 (VSS_1), IC1.35 (VSS_2), IC1.47 (VSS_3), R1.2, U$7.GROUND; also elsewhere on the board
I2C_SCL: IC1.46 (PB9); also elsewhere on the board
I2C_SDA: IC1.45 (PB8); also elsewhere on the board
IR_RECEIVE1: IC1.10 (PA0); also elsewhere on the board
IR_RECEIVE2: IC1.11 (PA1); also elsewhere on the board
IR_RECEIVE3: IC1.12 (PA2); also elsewhere on the board
IR_RECEIVE4: IC1.13 (PA3); also elsewhere on the board
IR_TRANSMIT: IC1.21 (PB10); also elsewhere on the board
unnamed: IC1.44 (BOOT0), R1.1
unnamed: C3.+, C4.1, IC1.9 (VDDA), L1.1
OSC_IN1: IC1.5 (PD0/OSC<=), U$7.INPUT
OSC_OUT1: IC1.6 (PD1/OSC=>), U$7.OUTPUT
RESET: IC1.7 (NRST); also elsewhere on the board
SHARP1: IC1.14 (PA4); also elsewhere on the board
SHARP2: IC1.15 (PA5); also elsewhere on the board
SONAR_ECHO_1: IC1.31 (PA10); also elsewhere on the board
SONAR_ECHO_2: IC1.29 (PA8); also elsewhere on the board
SONAR_TRIG_1: IC1.32 (PA11); also elsewhere on the board
SONAR_TRIG_2: IC1.30 (PA9); also elsewhere on the board
SPI_MISO: IC1.27 (PB14); also elsewhere on the board
SPI_MOSI: IC1.28 (PB15); also elsewhere on the board
SPI_NSS11: IC1.39 (PB3); also elsewhere on the board
SPI_NSS12: IC1.40 (PB4); also elsewhere on the board
SPI_NSS13: IC1.41 (PB5); also elsewhere on the board
SPI_SCK: IC1.26 (PB13); also elsewhere on the board
SWCLK1: IC1.37 (PA14); also elsewhere on the board
SWDIO1: IC1.34 (PA13); also elsewhere on the board
USART1_RX: IC1.43 (PB7); also elsewhere on the board
USART1_TX: IC1.42 (PB6); also elsewhere on the board
VDD: C7.1, C8.1, C9.1, IC1.1 (VBAT), IC1.24 (VDD_1), IC1.36 (VDD_2), IC1.48 (VDD_3); also elsewhere on the board
VDDA: L1.2; also elsewhere on the board

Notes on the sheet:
Filtrowanie uC
Wyprowadzenia uC
Zasilanie uC
Oscylator ceramiczny
Rozpiska sygnałów STM1:
- Wejście analogowe od Sharpów [ADC1, kanały 4,5,6,7,8,9]
- Wejście analogowe od Czujników Podłogi [ADC2, kanały 1,2,3,4]
- Sonary [TIM1 Kanały 1-PWM, 2-PWM, 3-IC,4-IC]
- Komunikacja USART [USART1Remap]
- Komunikacja SPI [SPI2]
- Linie programatora [SWD]
- Komunikacja I2C [I2C1Remap]
- CzujnikiIR [TIM2Remap Kanał 1-PWM]
- Komunikacja SPI [NSS - Podłączone gdziekolwiek - obsługa programowa]

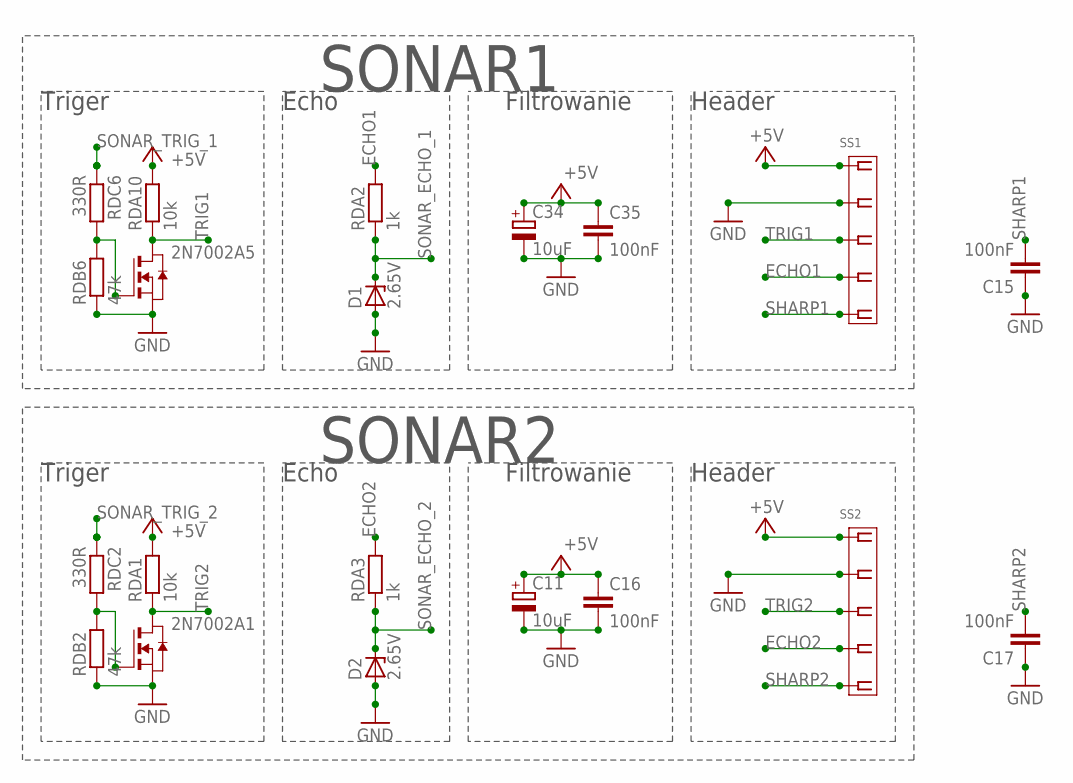
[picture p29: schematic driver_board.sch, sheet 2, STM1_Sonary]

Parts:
2N7002A1, 2N7002A5: NMOSSOT23; SOT-23
C11, C34: 10uF; SMC_A
C15, C16, C17, C35: 100nF; C0805
D1, D2: 2.65V; SOD80C
RDA1, RDA10: 10k; R0805
RDA2, RDA3: 1k; R0805
RDB2, RDB6: 47k; R0805
RDC2, RDC6: 330R; R0805
SS1, SS2: MOLEX-5268-05

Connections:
+5V: C11.+, C16.1, C34.+, C35.1, RDA1.2, RDA10.2, SS1.P$1 (1), SS2.P$1 (1); also elsewhere on the board
ECHO1: RDA2.2, SS1.P$4 (4)
ECHO2: RDA3.2, SS2.P$4 (4)
GND: 2N7002A1.2 (S), 2N7002A5.2 (S), C11.-, C15.1, C16.2, C17.1, C34.-, C35.2, D1.A, D2.A, RDB2.1, RDB6.1, SS1.P$2 (2), SS2.P$2 (2); also elsewhere on the board
unnamed: 2N7002A5.3 (G), RDB6.2, RDC6.2
unnamed: 2N7002A1.3 (G), RDB2.2, RDC2.2
SHARP1: C15.2, SS1.P$5 (5); also elsewhere on the board
SHARP2: C17.2, SS2.P$5 (5); also elsewhere on the board
SONAR_ECHO_1: D1.C, RDA2.1; also elsewhere on the board
SONAR_ECHO_2: D2.C, RDA3.1; also elsewhere on the board
SONAR_TRIG_1: RDC6.1; also elsewhere on the board
SONAR_TRIG_2: RDC2.1; also elsewhere on the board
TRIG1: 2N7002A5.1 (D), RDA10.1, SS1.P$3 (3)
TRIG2: 2N7002A1.1 (D), RDA1.1, SS2.P$3 (3)

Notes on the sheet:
Triger
Filtrowanie
Echo
SONAR1
Header
SONAR2

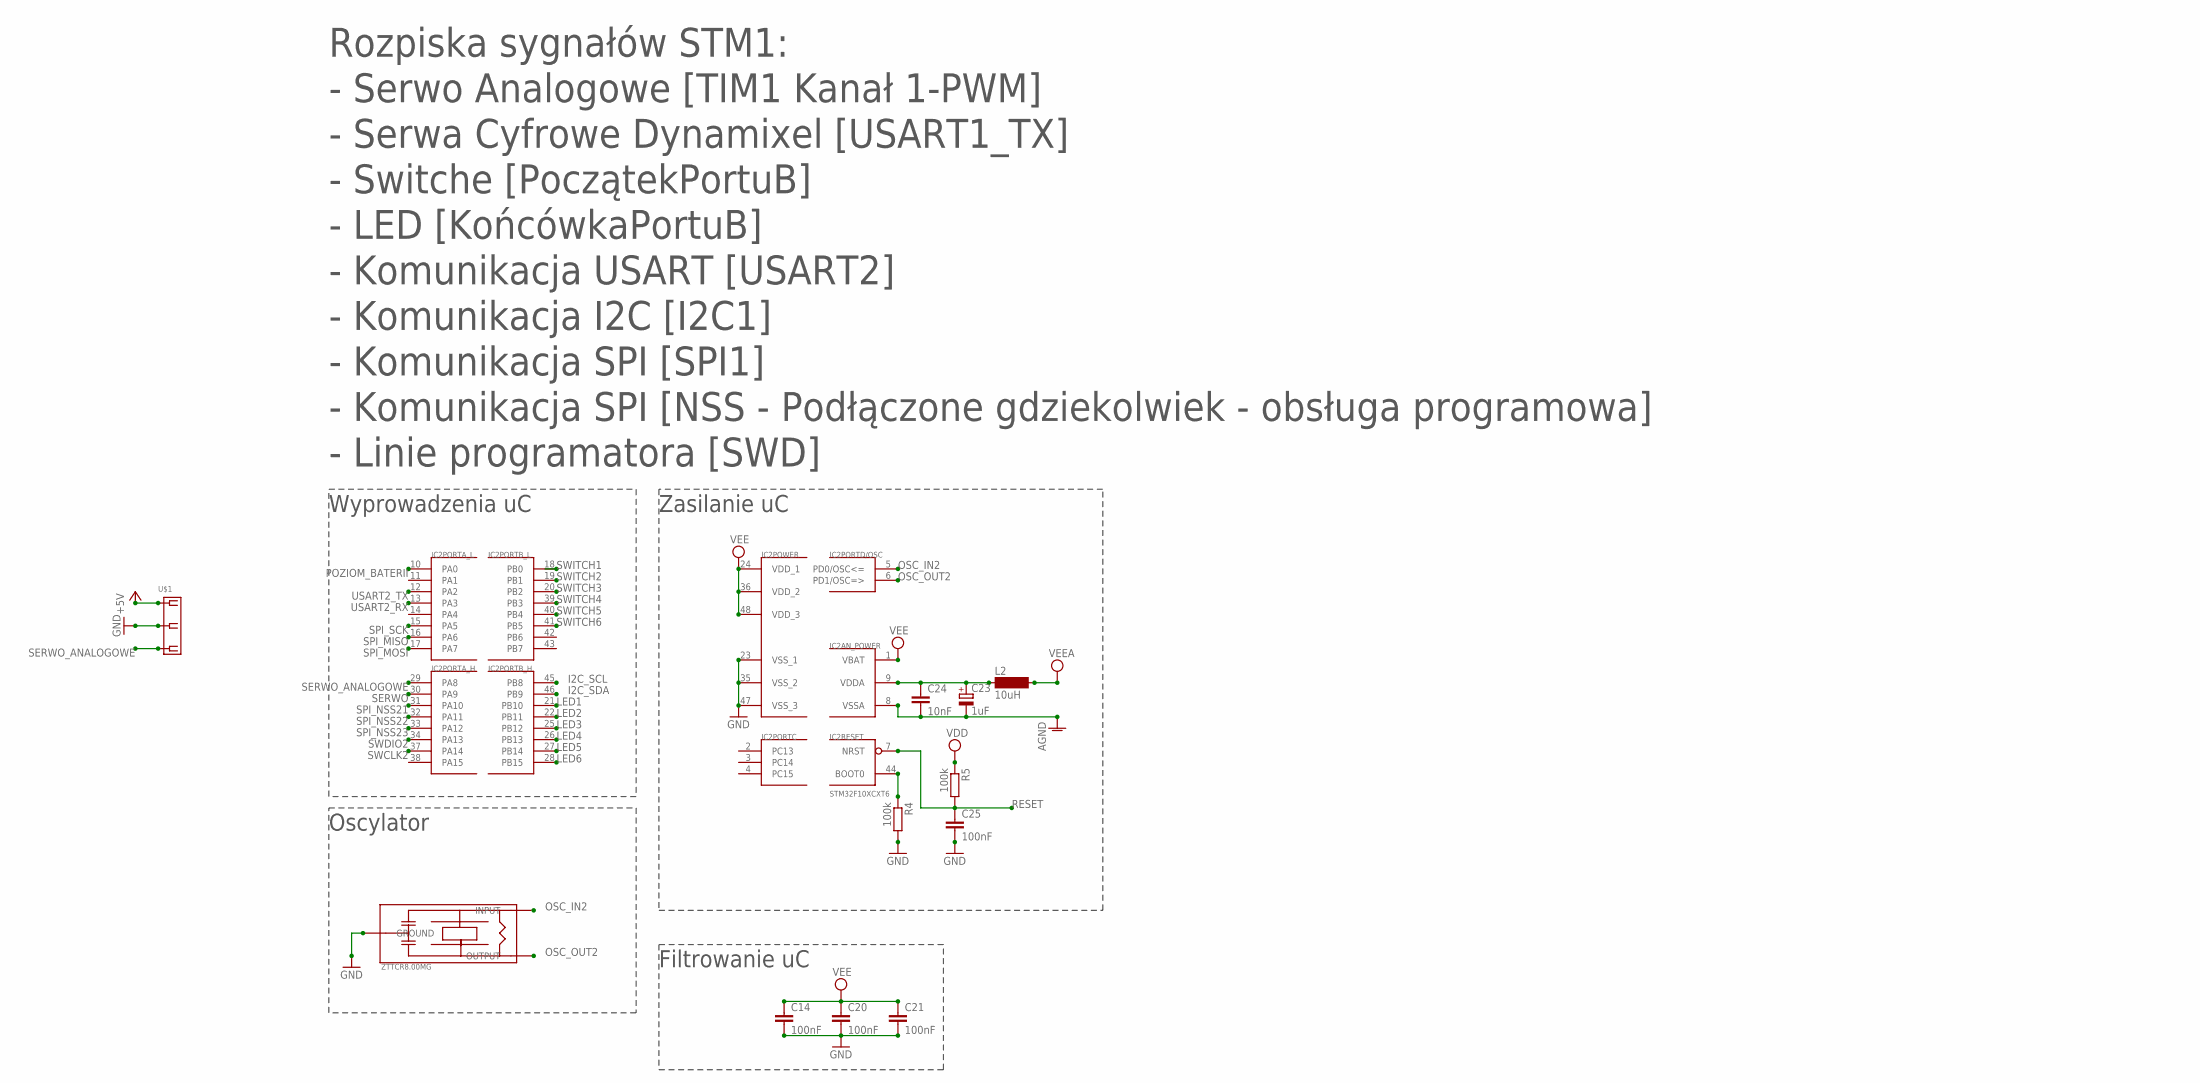
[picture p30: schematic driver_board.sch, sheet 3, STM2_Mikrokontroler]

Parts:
C14, C20, C21, C25: 100nF; C0805
C23: 1uF; SMC_A
C24: 10nF; C0805
IC2: STM32F10XCXT6; TQFP48
L2: 10uH; SM-1206
R4, R5: 100k; R0805
U$1: MOLEX-5268-03
U$8: ZTTCR8.00MG

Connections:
+5V: U$1.P$1 (1); also elsewhere on the board
AGND: C23.-, C24.2, IC2.8 (VSSA); also elsewhere on the board
GND: C14.2, C20.2, C21.2, C25.2, IC2.23 (VSS_1), IC2.35 (VSS_2), IC2.47 (VSS_3), R4.2, U$1.P$2 (2), U$8.GROUND; also elsewhere on the board
I2C_SCL: IC2.45 (PB8); also elsewhere on the board
I2C_SDA: IC2.46 (PB9); also elsewhere on the board
LED1: IC2.21 (PB10); also elsewhere on the board
LED2: IC2.22 (PB11); also elsewhere on the board
LED3: IC2.25 (PB12); also elsewhere on the board
LED4: IC2.26 (PB13); also elsewhere on the board
LED5: IC2.27 (PB14); also elsewhere on the board
LED6: IC2.28 (PB15); also elsewhere on the board
unnamed: C23.+, C24.1, IC2.9 (VDDA), L2.1
unnamed: IC2.44 (BOOT0), R4.1
OSC_IN2: IC2.5 (PD0/OSC<=), U$8.INPUT
OSC_OUT2: IC2.6 (PD1/OSC=>), U$8.OUTPUT
POZIOM_BATERII: IC2.10 (PA0); also elsewhere on the board
RESET: C25.1, IC2.7 (NRST), R5.2; also elsewhere on the board
SERWO: IC2.30 (PA9); also elsewhere on the board
SERWO_ANALOGOWE: IC2.29 (PA8), U$1.P$3 (3)
SPI_MISO: IC2.16 (PA6); also elsewhere on the board
SPI_MOSI: IC2.17 (PA7); also elsewhere on the board
SPI_NSS21: IC2.31 (PA10); also elsewhere on the board
SPI_NSS22: IC2.32 (PA11); also elsewhere on the board
SPI_NSS23: IC2.33 (PA12); also elsewhere on the board
SPI_SCK: IC2.15 (PA5); also elsewhere on the board
SWCLK2: IC2.37 (PA14); also elsewhere on the board
SWDIO2: IC2.34 (PA13); also elsewhere on the board
SWITCH1: IC2.18 (PB0); also elsewhere on the board
SWITCH2: IC2.19 (PB1); also elsewhere on the board
SWITCH3: IC2.20 (PB2); also elsewhere on the board
SWITCH4: IC2.39 (PB3); also elsewhere on the board
SWITCH5: IC2.40 (PB4); also elsewhere on the board
SWITCH6: IC2.41 (PB5); also elsewhere on the board
USART2_RX: IC2.13 (PA3); also elsewhere on the board
USART2_TX: IC2.12 (PA2); also elsewhere on the board
VDD: R5.1; also elsewhere on the board
VEE: C14.1, C20.1, C21.1, IC2.1 (VBAT), IC2.24 (VDD_1), IC2.36 (VDD_2), IC2.48 (VDD_3); also elsewhere on the board
VEEA: L2.2; also elsewhere on the board

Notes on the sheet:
Wyprowadzenia uC
Zasilanie uC
Oscylator
Filtrowanie uC
Rozpiska sygnałów STM1:
- Komunikacja USART [USART2]
- Komunikacja SPI [SPI1]
- Komunikacja SPI [NSS - Podłączone gdziekolwiek - obsługa programowa]
- Serwa Cyfrowe Dynamixel [USART1_TX]
- Serwo Analogowe [TIM1 Kanał 1-PWM]
- Komunikacja I2C [I2C1]
- Switche [PoczątekPortuB]
- LED [KońcówkaPortuB]
- Linie programatora [SWD]

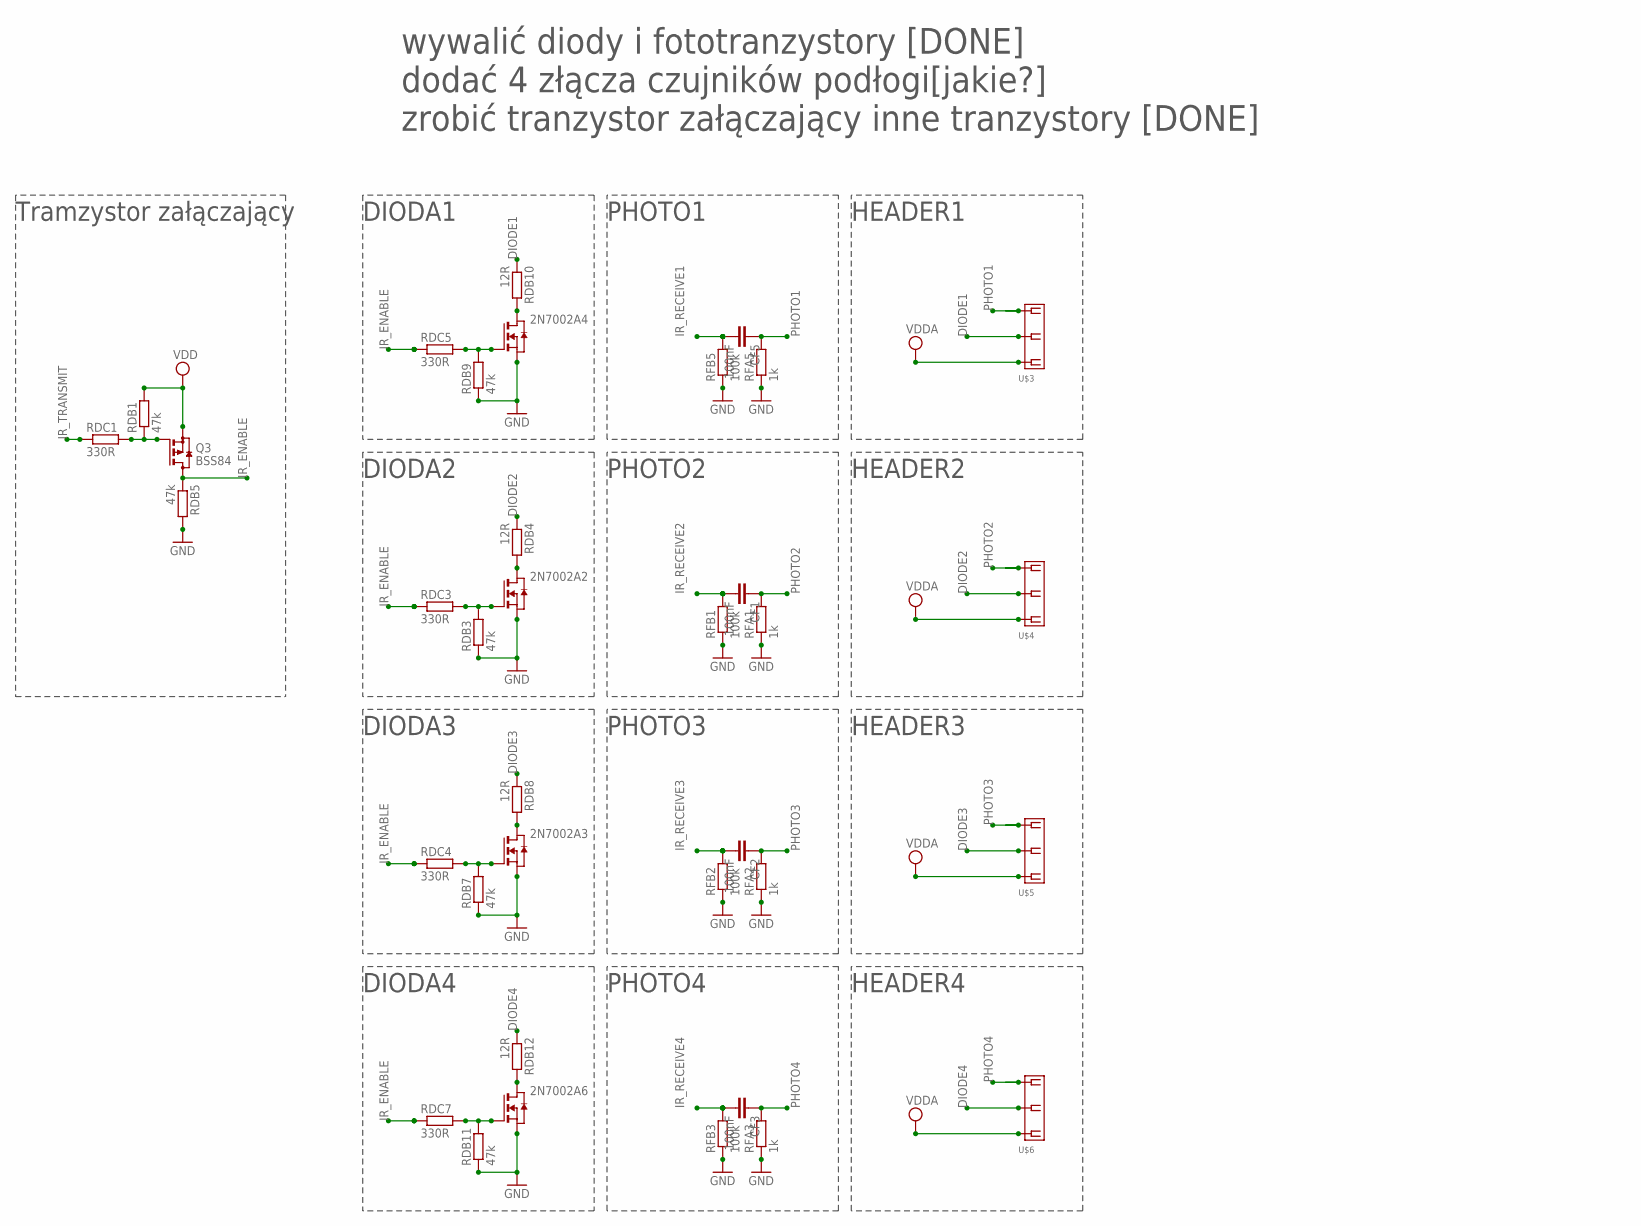
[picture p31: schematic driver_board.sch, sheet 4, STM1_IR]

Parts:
2N7002A2, 2N7002A3, 2N7002A4, 2N7002A6: NMOSSOT23; SOT-23
CF1, CF2, CF3, CF5: 100nF; C0805
Q3: BSS84; SOT23
RDB1, RDB3, RDB5, RDB7, RDB9, RDB11: 47k; R0805
RDB4, RDB8, RDB10, RDB12: 12R; R0805
RDC1, RDC3, RDC4, RDC5, RDC7: 330R; R0805
RFA1, RFA2, RFA3, RFA5: 1k; R0805
RFB1, RFB2, RFB3, RFB5: 100k; R0805
U$3, U$4, U$5, U$6: MOLEX-5268-03

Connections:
DIODE1: RDB10.1, U$3.P$2 (2)
DIODE2: RDB4.1, U$4.P$2 (2)
DIODE3: RDB8.1, U$5.P$2 (2)
DIODE4: RDB12.1, U$6.P$2 (2)
GND: 2N7002A2.2 (S), 2N7002A3.2 (S), 2N7002A4.2 (S), 2N7002A6.2 (S), RDB3.1, RDB5.2, RDB7.1, RDB9.1, RDB11.1, RFA1.1, RFA2.1, RFA3.1, RFA5.1, RFB1.1, RFB2.1, RFB3.1, RFB5.1; also elsewhere on the board
IR_ENABLE: Q3.3 (D), RDB5.1, RDC3.1, RDC4.1, RDC5.1, RDC7.1
IR_RECEIVE1: CF5.2, RFB5.2; also elsewhere on the board
IR_RECEIVE2: CF1.2, RFB1.2; also elsewhere on the board
IR_RECEIVE3: CF2.2, RFB2.2; also elsewhere on the board
IR_RECEIVE4: CF3.2, RFB3.2; also elsewhere on the board
IR_TRANSMIT: RDC1.1; also elsewhere on the board
unnamed: Q3.1 (G), RDB1.1, RDC1.2
unnamed: 2N7002A2.3 (G), RDB3.2, RDC3.2
unnamed: 2N7002A2.1 (D), RDB4.2
unnamed: 2N7002A3.3 (G), RDB7.2, RDC4.2
unnamed: 2N7002A3.1 (D), RDB8.2
unnamed: 2N7002A4.3 (G), RDB9.2, RDC5.2
unnamed: 2N7002A4.1 (D), RDB10.2
unnamed: 2N7002A6.3 (G), RDB11.2, RDC7.2
unnamed: 2N7002A6.1 (D), RDB12.2
PHOTO1: CF5.1, RFA5.2, U$3.P$3 (3)
PHOTO2: CF1.1, RFA1.2, U$4.P$3 (3)
PHOTO3: CF2.1, RFA2.2, U$5.P$3 (3)
PHOTO4: CF3.1, RFA3.2, U$6.P$3 (3)
VDD: Q3.2 (S), RDB1.2, U$3.P$1 (1), U$4.P$1 (1), U$5.P$1 (1), U$6.P$1 (1); also elsewhere on the board

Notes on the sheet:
zrobić tranzystor załączający inne tranzystory [DONE]
dodać 4 złącza czujników podłogi[jakie?]
wywalić diody i fototranzystory [DONE]
Tramzystor załączający
DIODA1
PHOTO1
HEADER1
DIODA2
PHOTO2
HEADER2
DIODA3
PHOTO3
HEADER3
DIODA4
PHOTO4
HEADER4

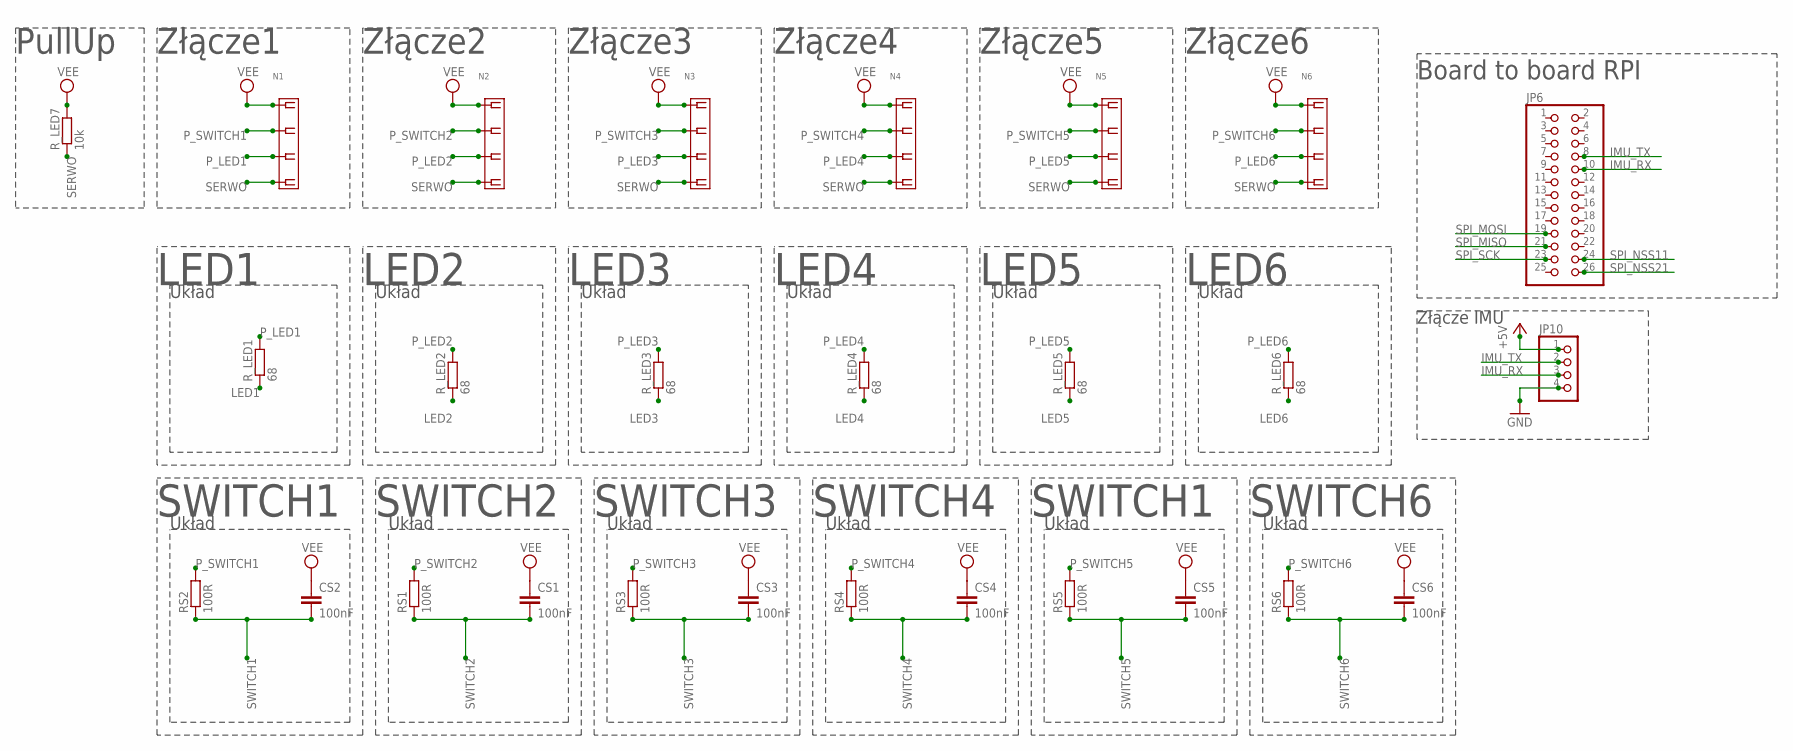
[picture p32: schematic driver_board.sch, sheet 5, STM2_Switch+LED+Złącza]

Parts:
CS1, CS2, CS3, CS4, CS5, CS6: 100nF; C0805
JP6: PINHD-2X13; 2X13
JP10: PINHD-1X4; 1X04
N1, N2, N3, N4, N5, N6: MOLEX-5268-04
RS1, RS2, RS3, RS4, RS5, RS6: 100R; R0805
R_LED1, R_LED2, R_LED3, R_LED4, R_LED5, R_LED6: 68; R0805
R_LED7: 10k; R1206

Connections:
+5V: JP10.1; also elsewhere on the board
GND: JP10.4; also elsewhere on the board
IMU_RX: JP6.10, JP10.3
IMU_TX: JP6.8, JP10.2
LED1: R_LED1.1; also elsewhere on the board
LED2: R_LED2.1; also elsewhere on the board
LED3: R_LED3.1; also elsewhere on the board
LED4: R_LED4.1; also elsewhere on the board
LED5: R_LED5.1; also elsewhere on the board
LED6: R_LED6.1; also elsewhere on the board
P_LED1: N1.P$3 (3), R_LED1.2
P_LED2: N2.P$3 (3), R_LED2.2
P_LED3: N3.P$3 (3), R_LED3.2
P_LED4: N4.P$3 (3), R_LED4.2
P_LED5: N5.P$3 (3), R_LED5.2
P_LED6: N6.P$3 (3), R_LED6.2
P_SWITCH1: N1.P$2 (2), RS2.2
P_SWITCH2: N2.P$2 (2), RS1.2
P_SWITCH3: N3.P$2 (2), RS3.2
P_SWITCH4: N4.P$2 (2), RS4.2
P_SWITCH5: N5.P$2 (2), RS5.2
P_SWITCH6: N6.P$2 (2), RS6.2
SERWO: N1.P$4 (4), N2.P$4 (4), N3.P$4 (4), N4.P$4 (4), N5.P$4 (4), N6.P$4 (4), R_LED7.1; also elsewhere on the board
SPI_MISO: JP6.21; also elsewhere on the board
SPI_MOSI: JP6.19; also elsewhere on the board
SPI_NSS11: JP6.24; also elsewhere on the board
SPI_NSS21: JP6.26; also elsewhere on the board
SPI_SCK: JP6.23; also elsewhere on the board
SWITCH1: CS2.2, RS2.1; also elsewhere on the board
SWITCH2: CS1.2, RS1.1; also elsewhere on the board
SWITCH3: CS3.2, RS3.1; also elsewhere on the board
SWITCH4: CS4.2, RS4.1; also elsewhere on the board
SWITCH5: CS5.2, RS5.1; also elsewhere on the board
SWITCH6: CS6.2, RS6.1; also elsewhere on the board
VEE: CS1.1, CS2.1, CS3.1, CS4.1, CS5.1, CS6.1, N1.P$1 (1), N2.P$1 (1), N3.P$1 (1), N4.P$1 (1), N5.P$1 (1), N6.P$1 (1), R_LED7.2; also elsewhere on the board

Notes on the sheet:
Układ
SWITCH1
LED1
LED2
LED3
LED4
LED5
LED6
Złącze1
SWITCH2
SWITCH3
SWITCH4
SWITCH6
PullUp
Board to board RPI
Złącze IMU
Złącze2
Złącze3
Złącze4
Złącze5
Złącze6

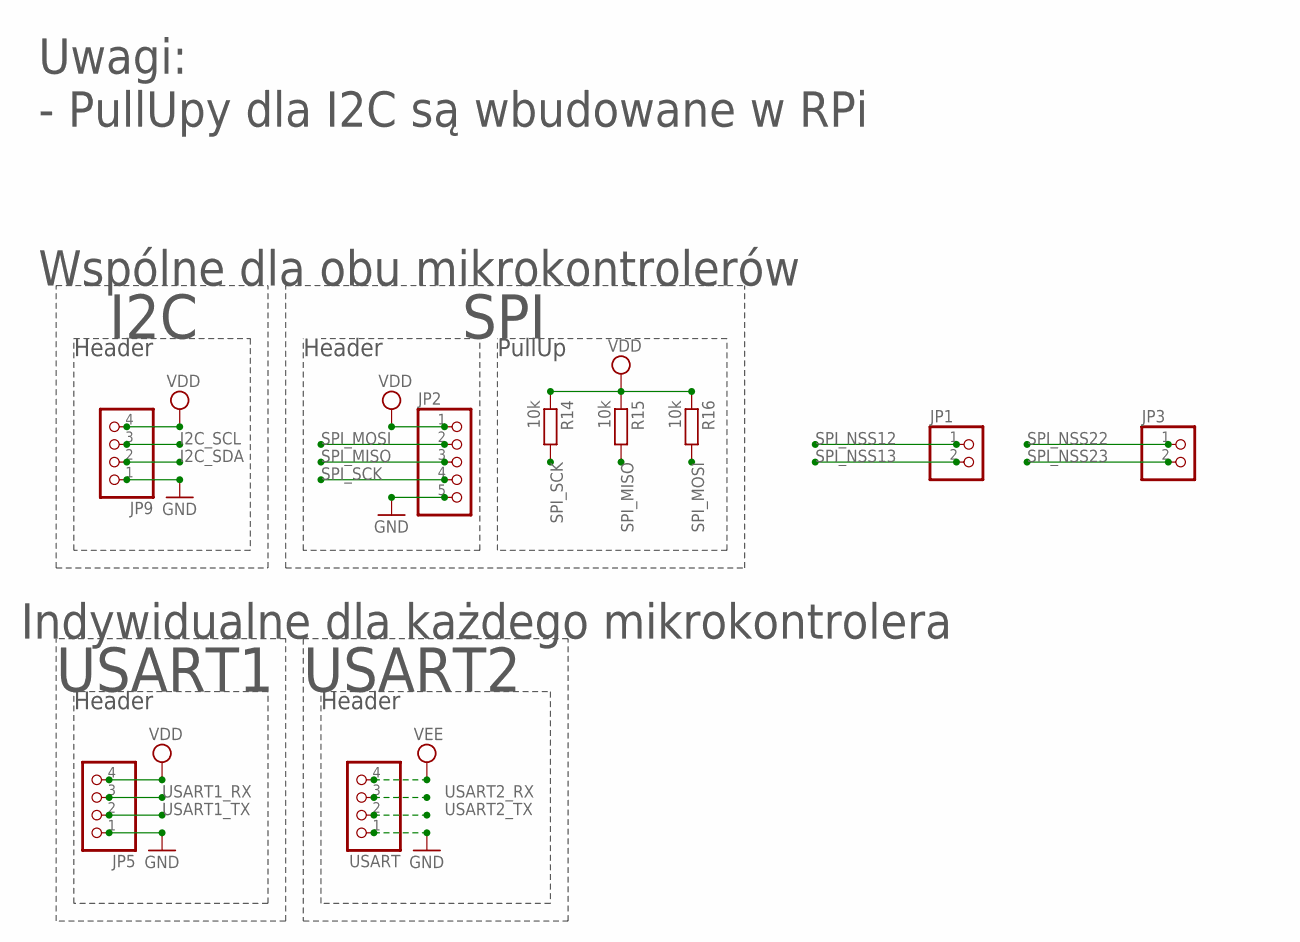
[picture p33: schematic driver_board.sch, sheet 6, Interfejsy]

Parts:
JP1, JP3: PINHD-1X2; 1X02
JP2: PINHD-1X5; 1X05
JP5, JP9: PINHD-1X4; 1X04
R14, R15, R16: 10k; R0805
USART: PINHD-1X4; 1X04

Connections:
GND: JP2.5, JP5.1, JP9.1, USART.1; also elsewhere on the board
I2C_SCL: JP9.3; also elsewhere on the board
I2C_SDA: JP9.2; also elsewhere on the board
SPI_MISO: JP2.3, R15.2; also elsewhere on the board
SPI_MOSI: JP2.2, R16.2; also elsewhere on the board
SPI_NSS12: JP1.1; also elsewhere on the board
SPI_NSS13: JP1.2; also elsewhere on the board
SPI_NSS22: JP3.1; also elsewhere on the board
SPI_NSS23: JP3.2; also elsewhere on the board
SPI_SCK: JP2.4, R14.2; also elsewhere on the board
USART1_RX: JP5.3; also elsewhere on the board
USART1_TX: JP5.2; also elsewhere on the board
USART2_RX: USART.3; also elsewhere on the board
USART2_TX: USART.2; also elsewhere on the board
VDD: JP2.1, JP5.4, JP9.4, R14.1, R15.1, R16.1; also elsewhere on the board
VEE: USART.4; also elsewhere on the board

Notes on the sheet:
Header
PullUp
I2C
SPI
USART1
Indywidualne dla każdego mikrokontrolera
Wspólne dla obu mikrokontrolerów
USART2
Uwagi:
- PullUpy dla I2C są wbudowane w RPi

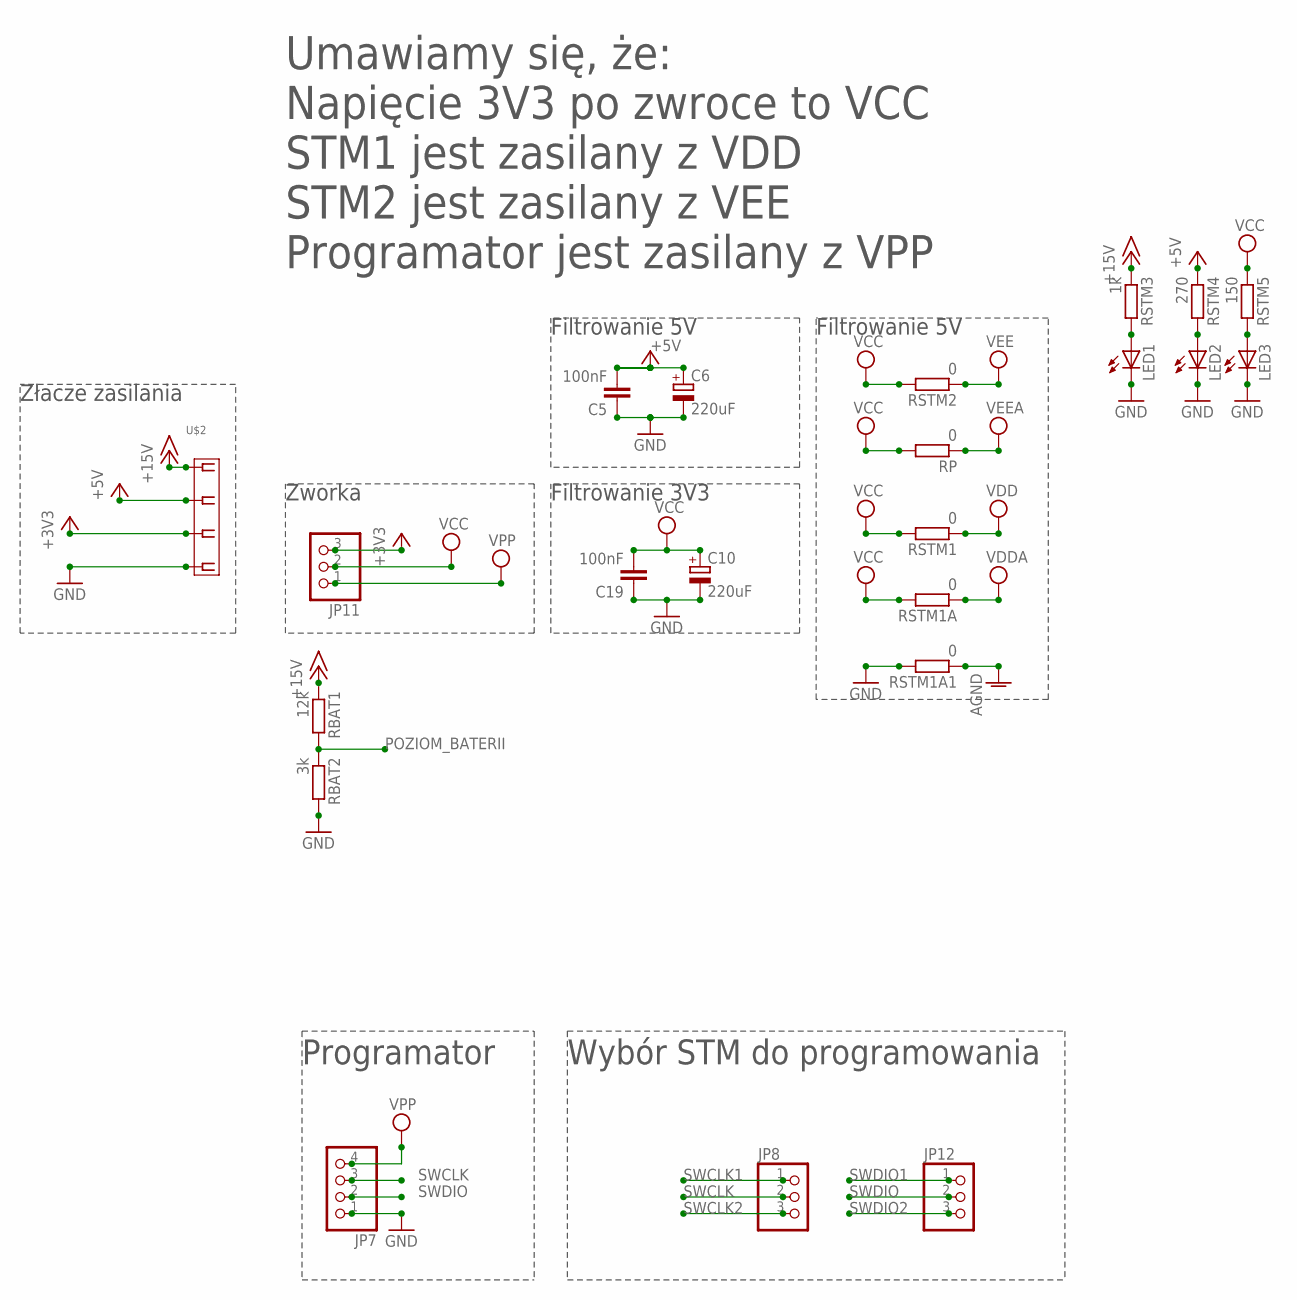
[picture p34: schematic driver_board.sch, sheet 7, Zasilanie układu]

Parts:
C5, C19: 100nF; C0805
C6, C10: 220uF; SMC_A
JP7: PINHD-1X4; 1X04
JP8, JP11, JP12: PINHD-1X3; 1X03
LED1, LED2, LED3: LEDCHIPLED_0805; CHIPLED_0805
RBAT1: 12k; R0805
RBAT2: 3k; R0805
RP: 0; R0805
RSTM1, RSTM1A, RSTM1A1, RSTM2: 0; R0805
RSTM3: 1k; R0805
RSTM4: 270; R0805
RSTM5: 150; R0805
U$2: MOLEX-5268-04

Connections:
+3V3: JP11.3, U$2.P$3 (3)
+5V: C5.2, C6.+, RSTM4.1, U$2.P$2 (2); also elsewhere on the board
+15V: RBAT1.1, RSTM3.1, U$2.P$1 (1)
AGND: RSTM1A1.1; also elsewhere on the board
GND: C5.1, C6.-, C10.-, C19.1, JP7.1, LED1.C, LED2.C, LED3.C, RBAT2.2, RSTM1A1.2, U$2.P$4 (4); also elsewhere on the board
unnamed: LED2.A, RSTM4.2
unnamed: LED3.A, RSTM5.2
unnamed: LED1.A, RSTM3.2
POZIOM_BATERII: RBAT1.2, RBAT2.1; also elsewhere on the board
SWCLK: JP7.3, JP8.2
SWCLK1: JP8.1; also elsewhere on the board
SWCLK2: JP8.3; also elsewhere on the board
SWDIO: JP7.2, JP12.2
SWDIO1: JP12.1; also elsewhere on the board
SWDIO2: JP12.3; also elsewhere on the board
VCC: C10.+, C19.2, JP11.2, RP.2, RSTM1.2, RSTM1A.2, RSTM2.2, RSTM5.1
VDD: RSTM1.1; also elsewhere on the board
VDDA: RSTM1A.1; also elsewhere on the board
VEE: RSTM2.1; also elsewhere on the board
VEEA: RP.1; also elsewhere on the board
VPP: JP7.4, JP11.1

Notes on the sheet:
Zworka
STM1 jest zasilany z VDD
STM2 jest zasilany z VEE
Umawiamy się, że:
Programator jest zasilany z VPP
Napięcie 3V3 po zwroce to VCC
Filtrowanie 5V
Filtrowanie 3V3
Programator
Wybór STM do programowania
Złacze zasilania

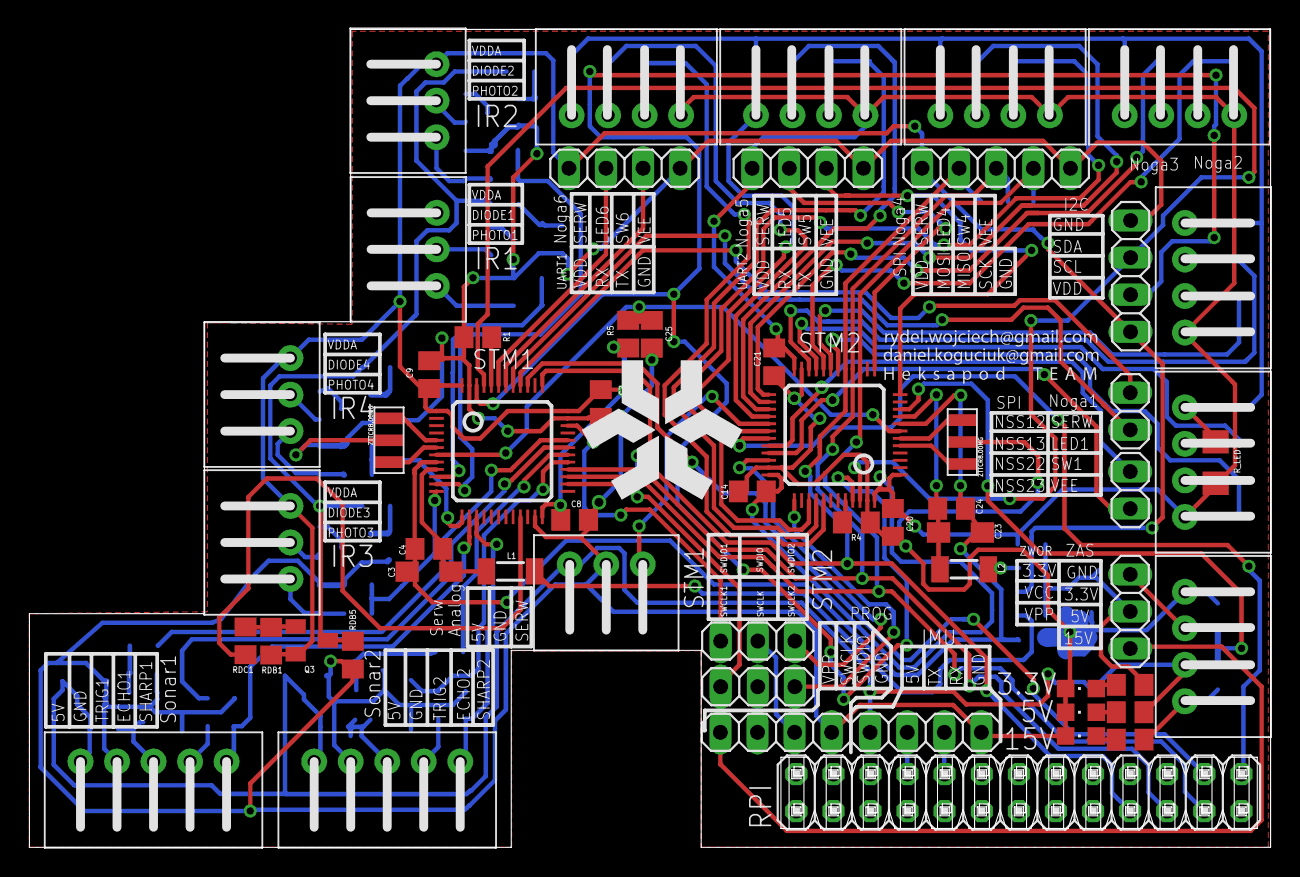
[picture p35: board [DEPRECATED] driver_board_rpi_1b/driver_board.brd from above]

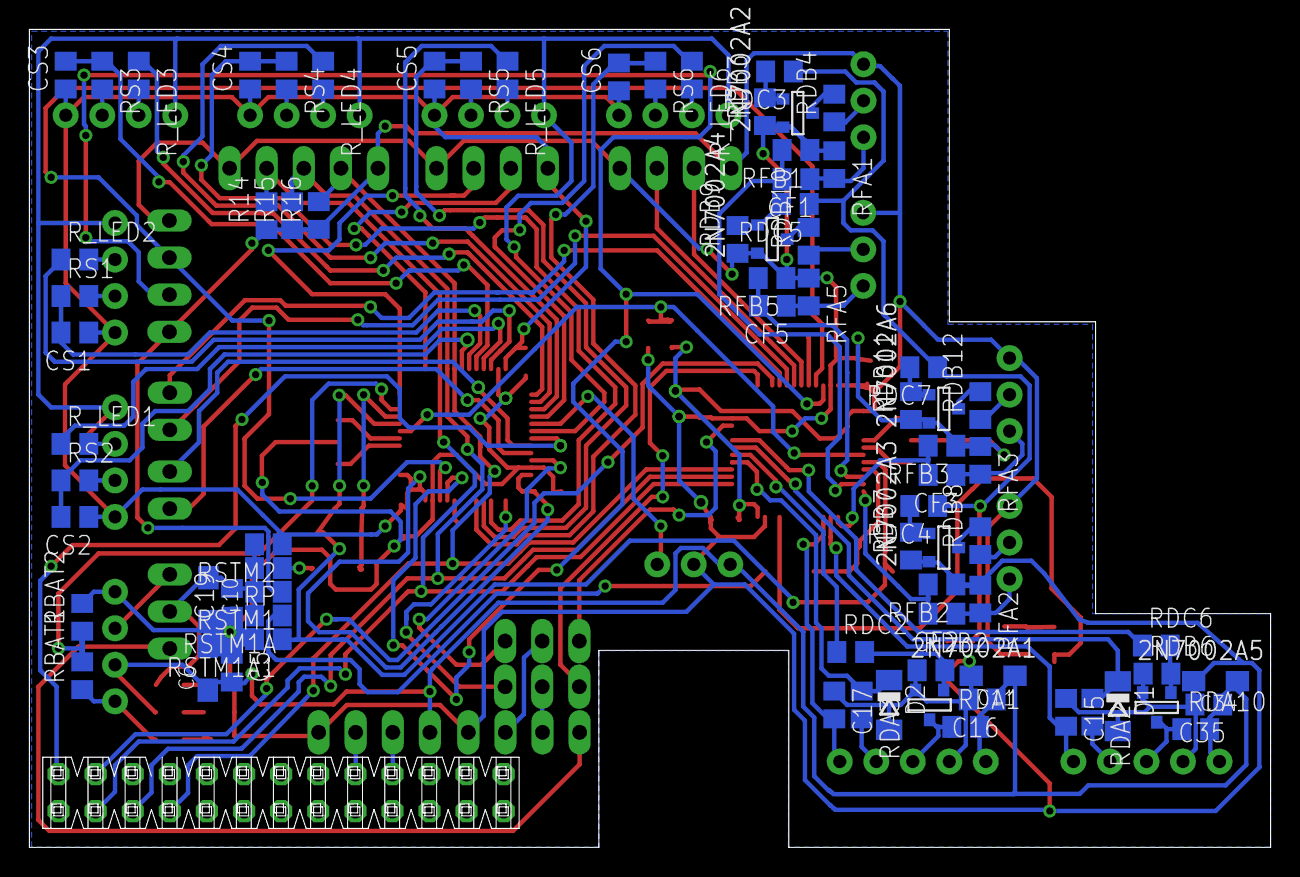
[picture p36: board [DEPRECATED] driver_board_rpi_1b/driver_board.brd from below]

Board: 2 copper layers, 85.0 x 56.0 mm, 135 parts (78 on the bottom side), 108 nets.

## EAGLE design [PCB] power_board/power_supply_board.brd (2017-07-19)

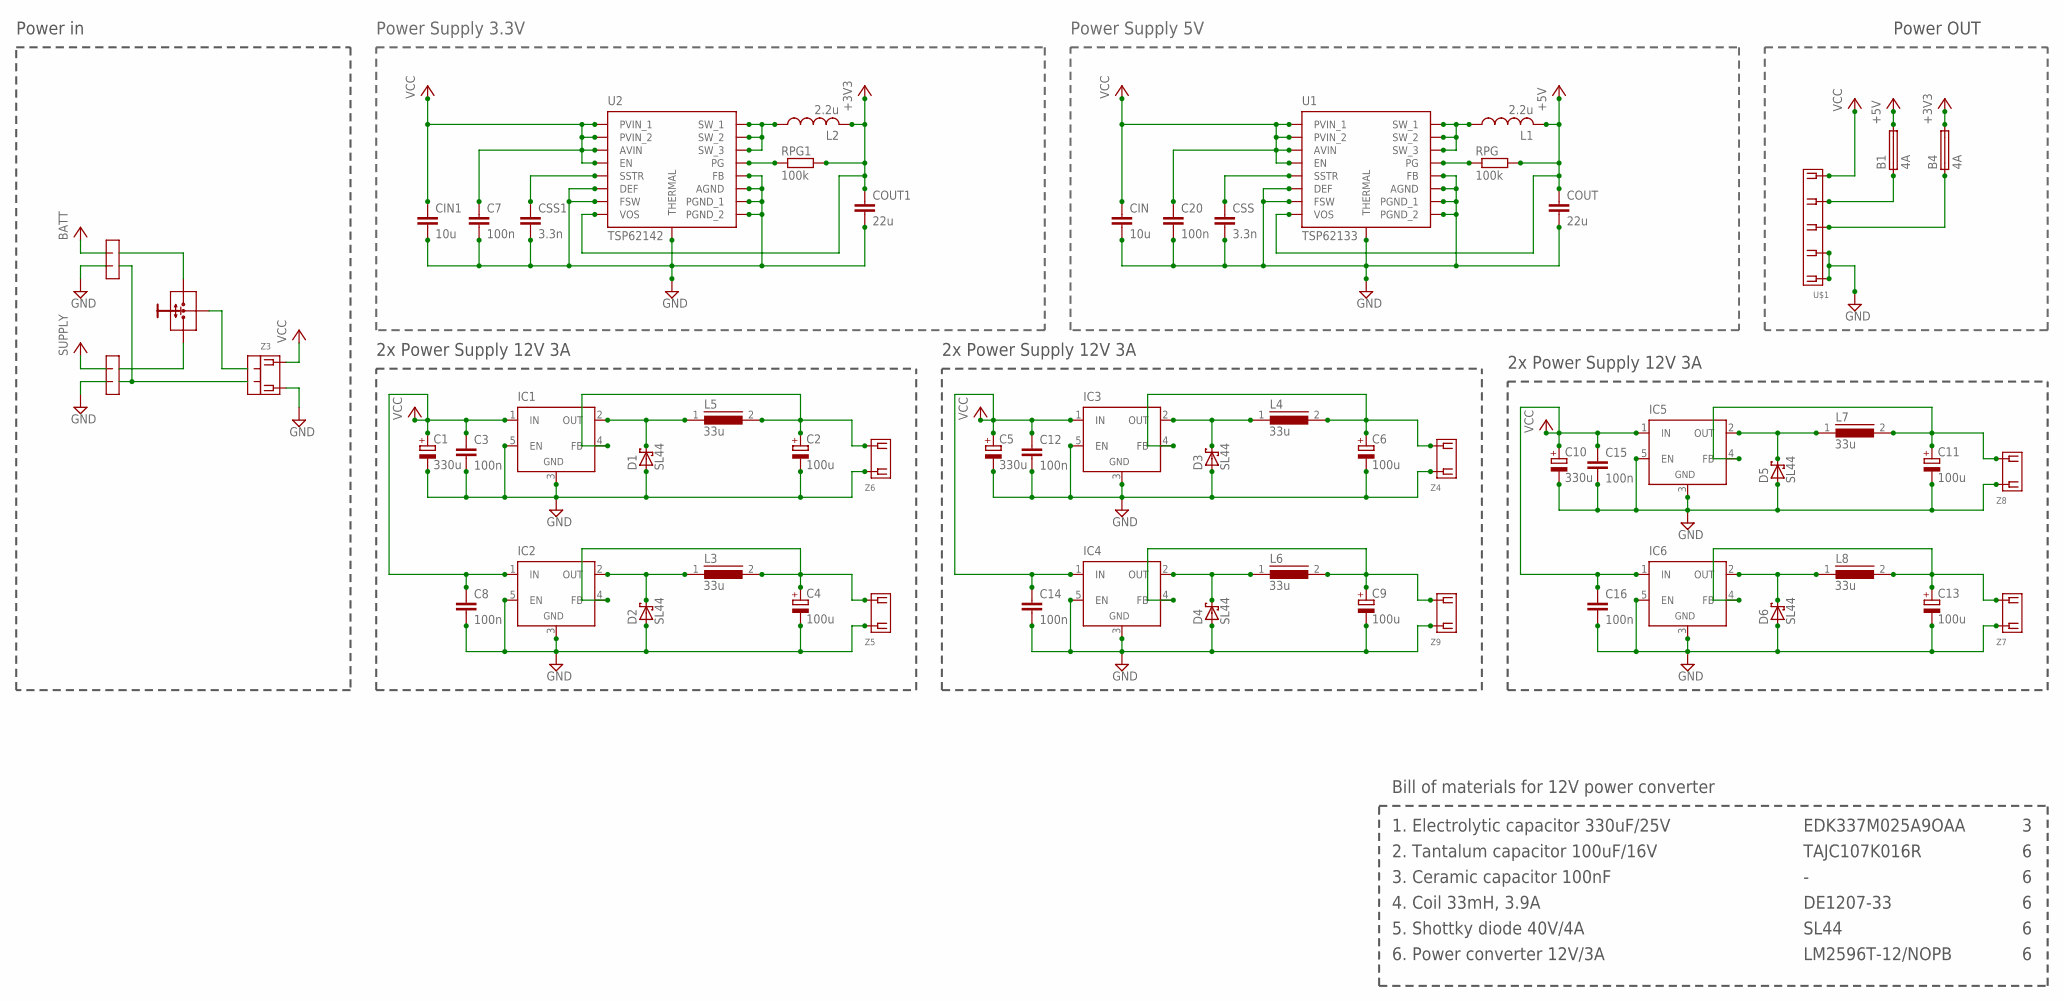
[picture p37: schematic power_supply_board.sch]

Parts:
B1, B4: 4A; 1206
C1, C5, C10: 330u; 150CLZ-1010
C2, C4, C6, C9, C11, C13: 100u; SMC_C
C3, C7, C8, C12, C14, C15, C16, C20: 100n; C0805
CIN, CIN1: 10u; C0805
COUT, COUT1: 22u; C0805
CSS, CSS1: 3.3n; C0805
D1, D2, D3, D4, D5, D6: SL44; SMC
IC1, IC2, IC3, IC4, IC5, IC6: LM2596TV; TO220-51
L1, L2: 2.2u; POWER-CHOKE_WE-TPC
L3, L4, L5, L6, L7, L8: 33u; DR127
RPG, RPG1: 100k; R0805
U1: TSP62133
U2: TSP62142
U$1: MOLEX-5268-05
Z3: 2EDGRC-5
Z4, Z5, Z6, Z7, Z8, Z9: MOLEX-5268-02

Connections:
12V3A_1: C2.+, IC1.4 (FB), L5.2, Z6.P$2 (2)
12V3A_2: C4.+, IC2.4 (FB), L3.2, Z5.P$2 (2)
12V3A_3: C6.+, IC3.4 (FB), L4.2, Z4.P$2 (2)
12V3A_4: C9.+, IC4.4 (FB), L6.2, Z9.P$2 (2)
12V3A_5: C11.+, IC5.4 (FB), L7.2, Z8.P$2 (2)
12V3A_6: C13.+, IC6.4 (FB), L8.2, Z7.P$2 (2)
+3V3: B4.2, COUT1.1, L2.2, RPG1.2, U2.VOS
+5V: B1.2, COUT.1, L1.2, RPG.2, U1.VOS
GND: C1.-, C2.-, C3.2, C4.-, C5.-, C6.-, C7.2, C8.2, C9.-, C10.-, C11.-, C12.2, C13.-, C14.2, C15.2, C16.2, C20.2, CIN.2, CIN1.2, COUT.2, COUT1.2, CSS.2, CSS1.2, D1.A, D2.A, D3.A, D4.A, D5.A, D6.A, IC1.3 (GND), IC1.5 (EN), IC2.3 (GND), IC2.5 (EN), IC3.3 (GND), IC3.5 (EN), IC4.3 (GND), IC4.5 (EN), IC5.3 (GND), IC5.5 (EN), IC6.3 (GND), IC6.5 (EN), U1.AGND, U1.DEF, U1.FB, U1.FSW, U1.PGND_1, U1.PGND_2, U1.THERMAL, U2.AGND, U2.DEF, U2.FB, U2.FSW, U2.PGND_1, U2.PGND_2, U2.THERMAL, U$1.P$1 (1), U$1.P$2 (2), Z3.P$2 (2), Z4.P$1 (1), Z5.P$1 (1), Z6.P$1 (1), Z7.P$1 (1), Z8.P$1 (1), Z9.P$1 (1)
unnamed: CSS.1, U1.SSTR
unnamed: L2.1, U2.SW_1, U2.SW_2, U2.SW_3
unnamed: RPG1.1, U2.PG
unnamed: CSS1.1, U2.SSTR
unnamed: D2.C, IC2.2 (OUT), L3.1
unnamed: D3.C, IC3.2 (OUT), L4.1
unnamed: L1.1, U1.SW_1, U1.SW_2, U1.SW_3
unnamed: D4.C, IC4.2 (OUT), L6.1
unnamed: RPG.1, U1.PG
unnamed: D5.C, IC5.2 (OUT), L7.1
unnamed: D6.C, IC6.2 (OUT), L8.1
unnamed: D1.C, IC1.2 (OUT), L5.1
unnamed: B1.1, U$1.P$4 (4)
unnamed: B4.1, U$1.P$3 (3)
VCC: C1.+, C3.1, C5.+, C7.1, C8.1, C10.+, C12.1, C14.1, C15.1, C16.1, C20.1, CIN.1, CIN1.1, IC1.1 (IN), IC2.1 (IN), IC3.1 (IN), IC4.1 (IN), IC5.1 (IN), IC6.1 (IN), U1.AVIN, U1.EN, U1.PVIN_1, U1.PVIN_2, U2.AVIN, U2.EN, U2.PVIN_1, U2.PVIN_2, U$1.P$5 (5), Z3.P$1 (1)

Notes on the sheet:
Power Supply 3.3V
Power in
Power OUT
2x Power Supply 12V 3A
Power Supply 5V
Bill of materials for 12V power converter
1. Electrolytic capacitor 330uF/25V
EDK337M025A9OAA
2. Tantalum capacitor 100uF/16V
TAJC107K016R
3. Ceramic capacitor 100nF
4. Coil 33mH, 3.9A
DE1207-33
5. Shottky diode 40V/4A
SL44
6. Power converter 12V/3A
LM2596T-12/NOPB

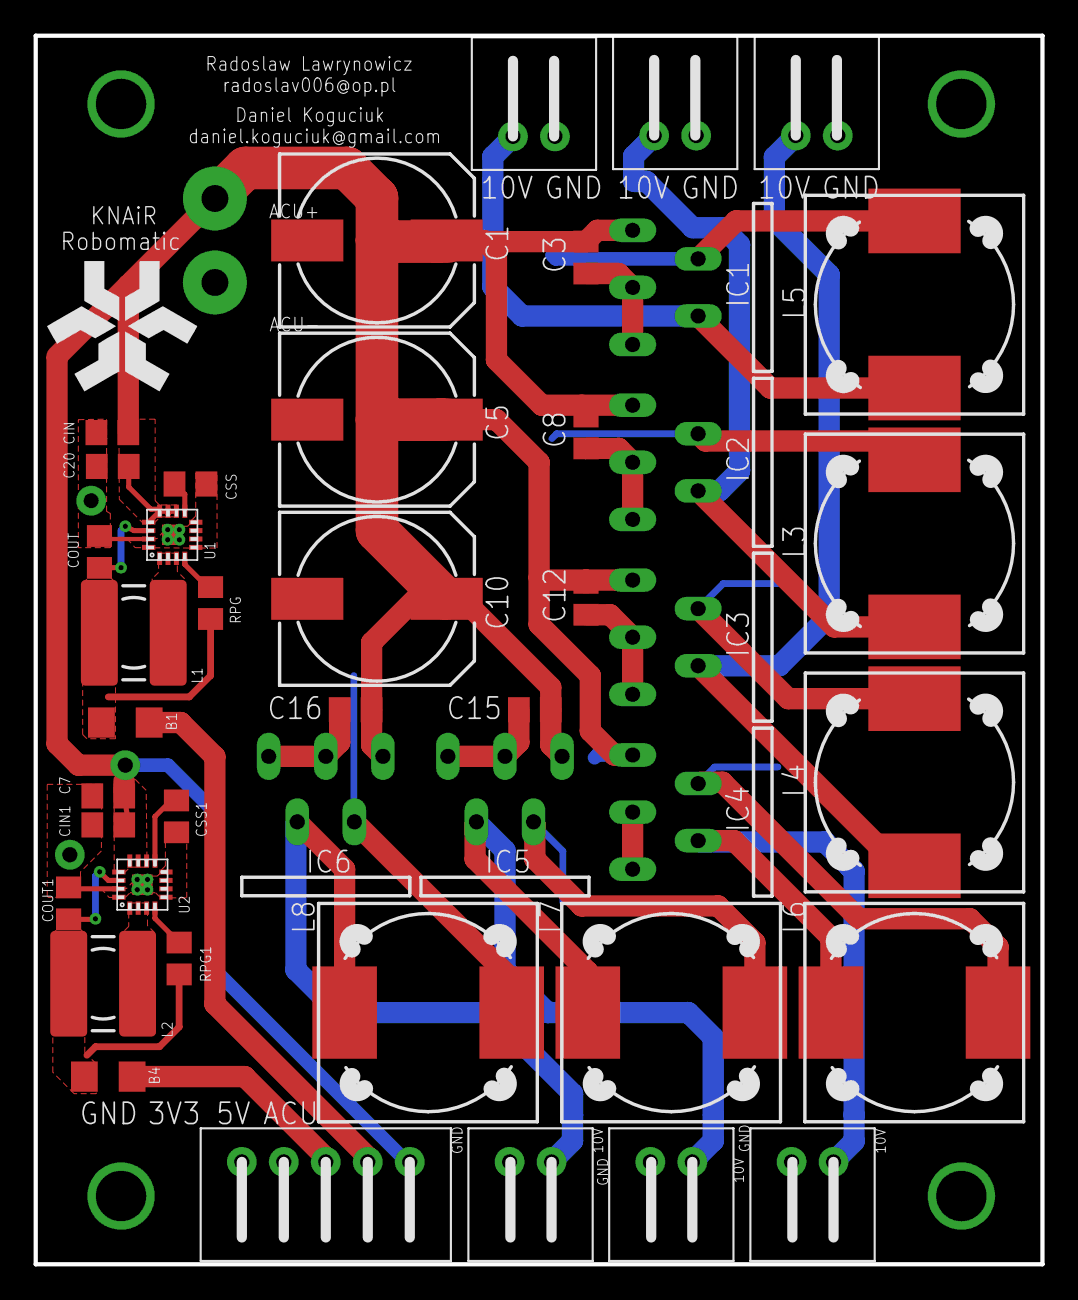
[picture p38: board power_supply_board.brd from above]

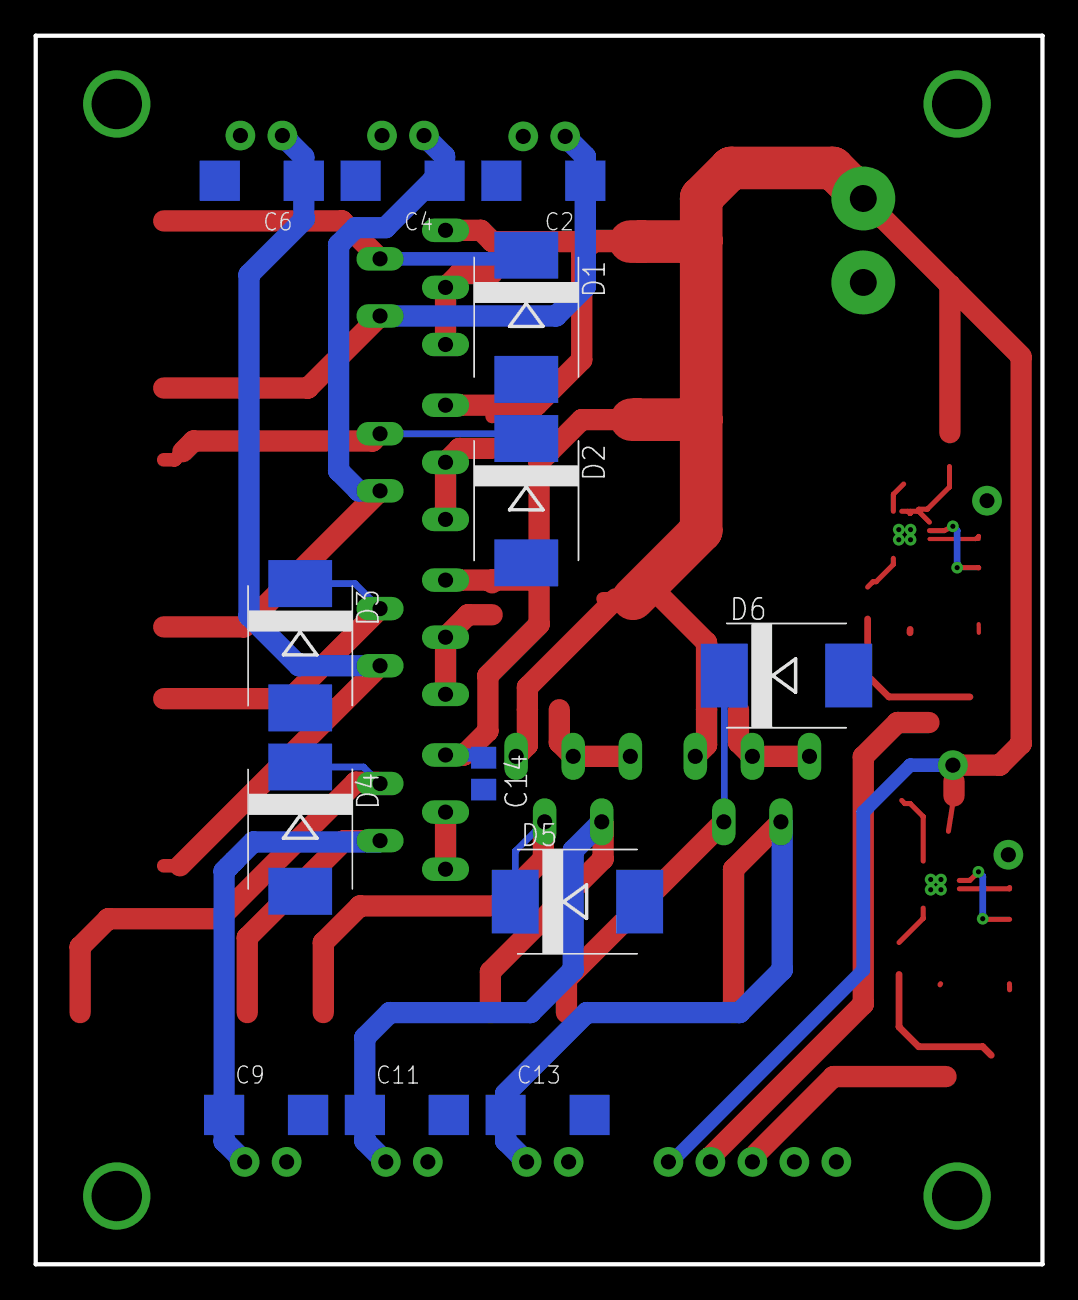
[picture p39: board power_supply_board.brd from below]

Board: 2 copper layers, 59.9 x 73.2 mm, 57 parts (13 on the bottom side), 24 nets.

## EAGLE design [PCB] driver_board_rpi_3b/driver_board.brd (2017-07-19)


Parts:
2N7002A5: NMOSSOT23; SOT-23
C15, C35: 100nF; C0805
C34: 10uF; SMC_A
D2: 2.65V; SOT23
R3: 47k; R0805
R6: 330R; R0805
R7: 10k; R0805
R8: 1k; R0805
SS1: MOLEX-5268-05

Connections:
+5V: C34.+, C35.1, R7.2, SS1.P$1 (1); also elsewhere on the board
ECHO: R8.2, SS1.P$4 (4)
GND: 2N7002A5.2 (S), C15.1, C34.-, C35.2, D2.1 (A), R3.1, SS1.P$2 (2); also elsewhere on the board
unnamed: 2N7002A5.3 (G), R3.2, R6.2
SHARP: C15.2, SS1.P$5 (5); also elsewhere on the board
SONAR_ECHO: D2.3 (C), R8.1; also elsewhere on the board
SONAR_TRIG: R6.1; also elsewhere on the board
TRIG: 2N7002A5.1 (D), R7.1, SS1.P$3 (3)

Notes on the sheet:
Triger
Filtrowanie
Echo
SONAR1
Header
Sharp1


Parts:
C14, C20, C21, C25: 100nF; C0805
C23: 1uF; SMC_A
C24: 10nF; C0805
IC2: STM32F10XCXT6; TQFP48
L2: 10uH; SM-1206
R1: 100; R0805
R4, R5: 100k; R0805
S1: TACT-6XX-SMD
U$8: ZTTCR8.00MG

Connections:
GND: C14.2, C20.2, C21.2, C23.-, C24.2, C25.2, IC2.8 (VSSA), IC2.23 (VSS_1), IC2.35 (VSS_2), IC2.47 (VSS_3), R4.2, S1.P$1 (1), U$8.GROUND; also elsewhere on the board
I2C_SCL: IC2.45 (PB8); also elsewhere on the board
I2C_SDA: IC2.46 (PB9); also elsewhere on the board
LED1: IC2.21 (PB10); also elsewhere on the board
LED2: IC2.22 (PB11); also elsewhere on the board
LED3: IC2.25 (PB12); also elsewhere on the board
LED4: IC2.26 (PB13); also elsewhere on the board
LED5: IC2.27 (PB14); also elsewhere on the board
LED6: IC2.28 (PB15); also elsewhere on the board
unnamed: R1.2, S1.P$3 (4)
unnamed: C23.+, C24.1, IC2.9 (VDDA), L2.1
unnamed: IC2.44 (BOOT0), R4.1
OSC_IN: IC2.5 (PD0/OSC<=), U$8.INPUT
OSC_OUT: IC2.6 (PD1/OSC=>), U$8.OUTPUT
POZIOM_BATERII: IC2.10 (PA0); also elsewhere on the board
RESET: C25.1, IC2.7 (NRST), R1.1, R5.2
SERWO: IC2.12 (PA2); also elsewhere on the board
SHARP: IC2.14 (PA4); also elsewhere on the board
SONAR_ECHO: IC2.13 (PA3); also elsewhere on the board
SONAR_TRIG: IC2.11 (PA1); also elsewhere on the board
SPI_MISO: IC2.16 (PA6); also elsewhere on the board
SPI_MOSI: IC2.17 (PA7); also elsewhere on the board
SPI_SCK: IC2.15 (PA5); also elsewhere on the board
SWCLK: IC2.37 (PA14); also elsewhere on the board
SWDIO: IC2.34 (PA13); also elsewhere on the board
SWITCH1: IC2.18 (PB0); also elsewhere on the board
SWITCH2: IC2.19 (PB1); also elsewhere on the board
SWITCH3: IC2.20 (PB2); also elsewhere on the board
SWITCH4: IC2.39 (PB3); also elsewhere on the board
SWITCH5: IC2.40 (PB4); also elsewhere on the board
SWITCH6: IC2.41 (PB5); also elsewhere on the board
USART_RX: IC2.31 (PA10); also elsewhere on the board
USART_TX: IC2.30 (PA9); also elsewhere on the board
VCC: C14.1, C20.1, C21.1, IC2.1 (VBAT), IC2.24 (VDD_1), IC2.36 (VDD_2), IC2.48 (VDD_3), L2.2, R5.1; also elsewhere on the board

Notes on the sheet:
Wyprowadzenia uC
Zasilanie uC
Oscylator
Filtrowanie uC
Rozpiska sygnałów STM1:
- Komunikacja USART [USART1]
- Komunikacja SPI [SPI1]
- Serwa Cyfrowe Dynamixel [USART2_TX]
- Komunikacja I2C [I2C1 Remapped]
- Switche [PoczątekPortuB]
- LED [KońcówkaPortuB]
- Linie programatora [SWD]
- Poziom baterii [ADC]
- Sonar [TIM1 Kanał 2 - PWM, Kanał 3 - IC]
- Sharp [ADC]


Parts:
CS1, CS2, CS3, CS4, CS5, CS6: 100nF; C0805
JP3: PINHD-2X20; 2X20
N1, N2, N3, N4, N5, N6, N7: MOLEX-5268-04
R21, R22, R23, R24, R25, R26: 68; R0805
R27: 10k; R0805
RS1, RS2, RS3, RS4, RS5, RS6: 100R; R0805

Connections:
+5V: N7.P$1 (1); also elsewhere on the board
GND: JP3.25, N7.P$4 (4); also elsewhere on the board
IMU_RX: JP3.10, N7.P$3 (3)
IMU_TX: JP3.8, N7.P$2 (2)
LED1: R21.1; also elsewhere on the board
LED2: R22.1; also elsewhere on the board
LED3: R23.1; also elsewhere on the board
LED4: R24.1; also elsewhere on the board
LED5: R25.1; also elsewhere on the board
LED6: R26.1; also elsewhere on the board
P_LED1: N1.P$3 (3), R21.2
P_LED2: N2.P$3 (3), R22.2
P_LED3: N3.P$3 (3), R23.2
P_LED4: N4.P$3 (3), R24.2
P_LED5: N5.P$3 (3), R25.2
P_LED6: N6.P$3 (3), R26.2
P_SWITCH1: N1.P$2 (2), RS2.2
P_SWITCH2: N2.P$2 (2), RS1.2
P_SWITCH3: N3.P$2 (2), RS3.2
P_SWITCH4: N4.P$2 (2), RS4.2
P_SWITCH5: N5.P$2 (2), RS5.2
P_SWITCH6: N6.P$2 (2), RS6.2
SERWO: N1.P$4 (4), N2.P$4 (4), N3.P$4 (4), N4.P$4 (4), N5.P$4 (4), N6.P$4 (4), R27.1; also elsewhere on the board
SPI_MISO: JP3.21; also elsewhere on the board
SPI_MOSI: JP3.19; also elsewhere on the board
SPI_SCK: JP3.23; also elsewhere on the board
SWITCH1: CS2.2, RS2.1; also elsewhere on the board
SWITCH2: CS1.2, RS1.1; also elsewhere on the board
SWITCH3: CS3.2, RS3.1; also elsewhere on the board
SWITCH4: CS4.2, RS4.1; also elsewhere on the board
SWITCH5: CS5.2, RS5.1; also elsewhere on the board
SWITCH6: CS6.2, RS6.1; also elsewhere on the board
VCC: CS1.1, CS2.1, CS3.1, CS4.1, CS5.1, CS6.1, N1.P$1 (1), N2.P$1 (1), N3.P$1 (1), N4.P$1 (1), N5.P$1 (1), N6.P$1 (1), R27.2; also elsewhere on the board

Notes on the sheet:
Układ
SWITCH1
LED1
LED2
LED3
LED4
LED5
LED6
Złącze1
SWITCH2
SWITCH3
SWITCH4
SWITCH6
PullUp
Złącze2
Złącze3
Złącze4
Złącze5
Złącze6
IMU


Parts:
JP2: PINHD-1X5; 1X05
JP5, JP9: PINHD-1X4; 1X04

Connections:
GND: JP2.5, JP5.1, JP9.1; also elsewhere on the board
I2C_SCL: JP9.3; also elsewhere on the board
I2C_SDA: JP9.2; also elsewhere on the board
SPI_MISO: JP2.3; also elsewhere on the board
SPI_MOSI: JP2.2; also elsewhere on the board
SPI_SCK: JP2.4; also elsewhere on the board
USART_RX: JP5.3; also elsewhere on the board
USART_TX: JP5.2; also elsewhere on the board
VCC: JP2.1, JP5.4, JP9.4; also elsewhere on the board

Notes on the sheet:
Header
I2C
SPI
USART
Uwagi:
- PullUpy dla I2C są wbudowane w RPi


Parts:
C5, C19: 100nF; C0805
C6, C10: 220uF; SMC_A
JP7: PINHD-1X4; 1X04
JP11: PINHD-1X3; 1X03
LED1, LED2, LED3: LEDCHIPLED_0805; CHIPLED_0805
R9: 12k; R0805
R10: 3k; R0805
R11: 150; R0805
R12: 1k; R0805
R13: 270; R0805
U$1: MOLEX-5268-05

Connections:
+3V3: JP11.3, U$1.P$3 (3)
+5V: C5.2, C6.+, R13.1, U$1.P$2 (2); also elsewhere on the board
+15V: R9.1, R12.1, U$1.P$1 (1)
GND: C5.1, C6.-, C10.-, C19.1, JP7.1, LED1.C, LED2.C, LED3.C, R10.2, U$1.P$4 (4), U$1.P$5 (5); also elsewhere on the board
unnamed: LED2.A, R13.2
unnamed: LED3.A, R11.2
unnamed: LED1.A, R12.2
POZIOM_BATERII: R9.2, R10.1; also elsewhere on the board
SWCLK: JP7.3; also elsewhere on the board
SWDIO: JP7.2; also elsewhere on the board
VCC: C10.+, C19.2, JP11.2, R11.1; also elsewhere on the board
VPP: JP7.4, JP11.1

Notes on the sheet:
Zworka
Programator jest zasilany z VPP
Napięcie 3V3 po zwroce to VCC
Filtrowanie 5V
Filtrowanie 3V3
Programator
Złacze zasilania
LED
BAT



Board: 2 copper layers, 65.0 x 55.9 mm, 68 parts (20 on the bottom side), 58 nets.

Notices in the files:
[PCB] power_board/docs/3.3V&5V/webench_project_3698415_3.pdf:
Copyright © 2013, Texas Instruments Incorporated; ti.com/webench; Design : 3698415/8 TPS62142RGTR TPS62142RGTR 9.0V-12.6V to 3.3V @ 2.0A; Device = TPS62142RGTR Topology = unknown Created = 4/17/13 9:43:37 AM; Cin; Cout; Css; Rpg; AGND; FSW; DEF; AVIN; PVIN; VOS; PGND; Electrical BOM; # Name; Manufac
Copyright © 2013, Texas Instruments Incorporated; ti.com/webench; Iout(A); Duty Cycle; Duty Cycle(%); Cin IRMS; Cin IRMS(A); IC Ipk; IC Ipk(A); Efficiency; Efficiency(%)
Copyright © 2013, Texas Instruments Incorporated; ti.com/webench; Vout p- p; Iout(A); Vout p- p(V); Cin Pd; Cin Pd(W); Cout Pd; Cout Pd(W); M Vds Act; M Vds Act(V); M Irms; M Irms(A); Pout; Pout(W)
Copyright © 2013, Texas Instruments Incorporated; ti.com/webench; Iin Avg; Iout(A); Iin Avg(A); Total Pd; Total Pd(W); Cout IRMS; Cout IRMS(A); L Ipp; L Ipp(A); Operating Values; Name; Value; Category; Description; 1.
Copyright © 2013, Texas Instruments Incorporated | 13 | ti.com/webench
